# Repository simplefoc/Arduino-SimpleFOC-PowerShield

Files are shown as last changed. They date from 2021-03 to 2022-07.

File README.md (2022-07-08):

# Arduino *Simple**FOC** PowerShield* *v0.2* 
A powerful arduino shield for running BLDC motors using the FOC algorithm. This board is based on the [BTN8982](https://www.infineon.com/dgdl/Infineon-BTN8982TA-DS-v01_00-EN.pdf?fileId=db3a30433fa9412f013fbe32289b7c17) half bridges and can support currents up to 30 Amps continuous and 50Amps peak. Making it a board that can run virtually any BLDC motor.

<p align="">
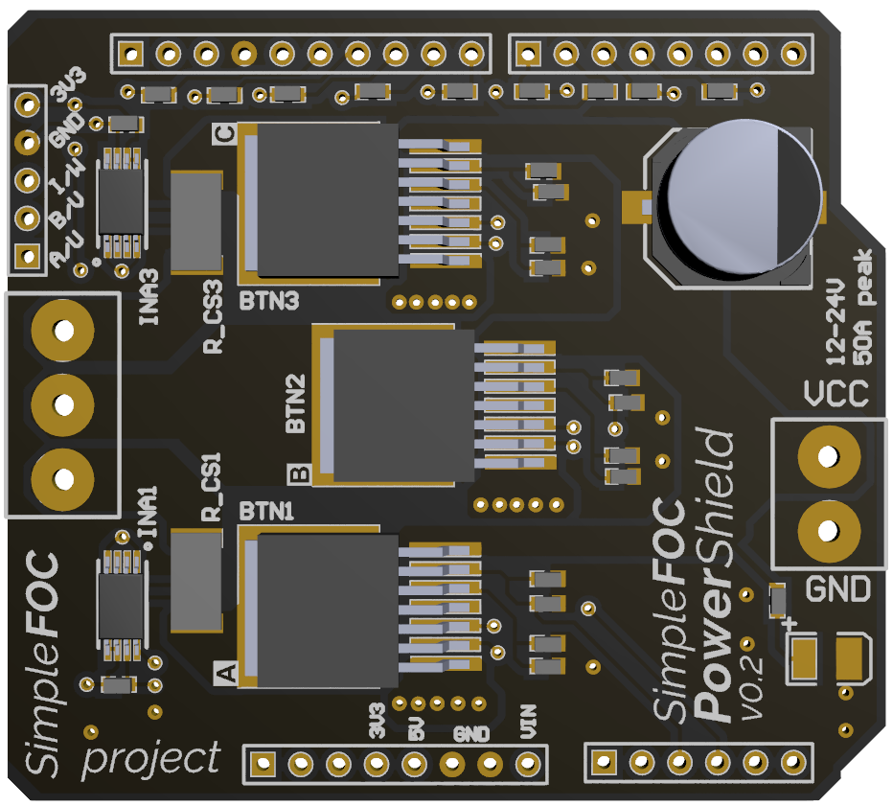
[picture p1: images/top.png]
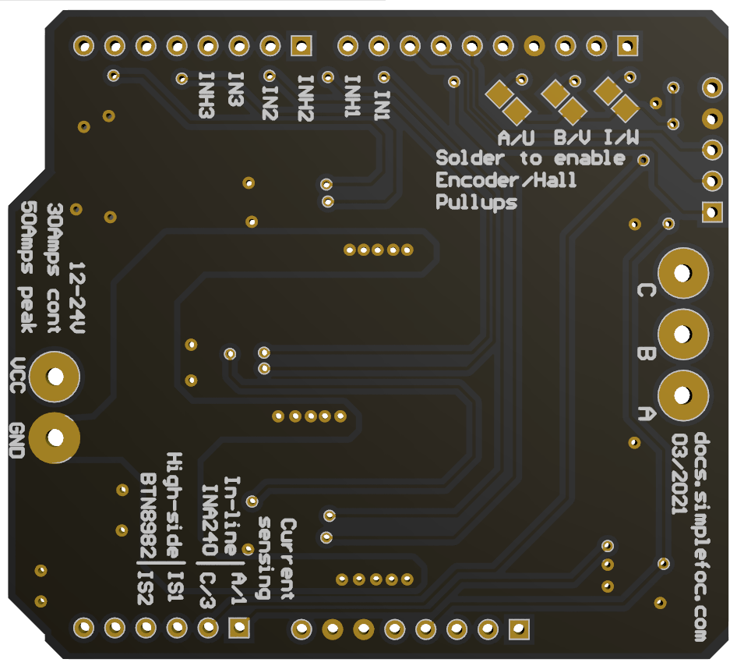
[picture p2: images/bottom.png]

</p>

<blockquote class="warning"><p class="heading"> ⚠️ BEWARE: BTN8982/IFX007T performance issues</p><p>BTN8982 and IFX007T drivers have been designed for DC motors and are based on old H-bridge technology. They have very long mosfet rise time (multiple microseconds) which in many cases presents a considerable part of the PWM duty cycle. When running the BLDC motors, precise PWM duty cycle setting is crucial for smooth and efficient operation. Therefore these drivers will not be able to provide very smooth operation on high frequency PWM (above 15kHz). Read more about it in the community thread: <a href="https://community.simplefoc.com/t/simplefoc-powershield/582">link</a>.<br> This performance constraint is the main reason why the <span class="simple">Simple<span class="foc">FOC</span> <b>Power</b>Shield</span> project has for now been put on hold, and although these boards are available through Aliexpress and some other platforms, they will not be available through simplefoc.com. <br><br></p><p>This does not mean that the board itself is not functional or that it will not work in your project though. It is still one of the cheapest (simplest) solutions out there for mid to high power BLDC control and with proper tuning of control loops you will still be able to get some good results with it.</p></blockquote>

### Features
- **Plug & play**: In combination with Arduino *Simple**FOC**library* - [github](https://github.com/simplefoc/Arduino-FOC)
- **Low-cost**: Fabrication price under €25/pcs - **will not be sold by silplefoc.com**
- **High-side current sensing**: - not yet supported by *Simple**FOC**library*
- **In-line current sensing**: - supported by *Simple**FOC**library*
- **Max power <500W**: max current 30A, power-supply 24V
- **Arduino headers**: Arduino UNO, Arduino MEGA, STM32 Nucleo boards, Aruidno DUE...
- **Small size**: 53mm x 60mm
- **Encoder/Hall sensors interface**: Integrated 3.3kΩ pullups (configurable)
- **Open Source**: 
   - Fully available fabrication files  
        - If never done it before, see a similar guide for *Simple**FOC**Shield*:  [how to make it yourself](https://docs.simplefoc.com/arduino_simplefoc_shield_fabrication)
   - Altium project
   - 3d model
   - schematics
    
#### Future features
- **Stackable**: running 2 motors in the same time
- **I2C interface**: Integrated 4.7kΩ pullups (configurable)
- **Configurable pinout**: Hardware configuration - soldering connections

> New version of the *Simple**FOC** PowerShield* is in the development at the moment (*v0.3*).
> The first versions are currently in testing. For more info check the [developmental branch](https://github.com/simplefoc/Arduino-SimpleFOC-PowerShield/tree/dev) 

### Pinouts
At this point ***Power**Shield* has fixed pinout.

#### Driver pinout
Signal | Description | Pin number
--- | --- | ----
IN1 | pwm 1 |	9
IN2 |  pwm 2 |	6
IN3 | 	pwm 3	 | 5 
INH1| enable 1 |	8
INH2 |	enable 2 |	7
INH3 |	enable  3	| 4

#### Current sensing pinout
Signal | Description | Pin number
--- | --- | ----
CS1 | in-line current sense - phase 1/A| A0
CS2 | in-line current sense - phase 3/C | A1
IS1 | high-side current sense - phase 1/A | A2
IS2 | high-side current sense - phase 2/B | A3

#### Sensor input pinout
Signal | Description | Pin number
--- | --- | ----
A/ U | Encoder A, Hall sensor U |	10
B/ V | Encoder B, Hall sensor V |	11
I/ W | Encoder C, Hall sensor W |	12

<p align="">
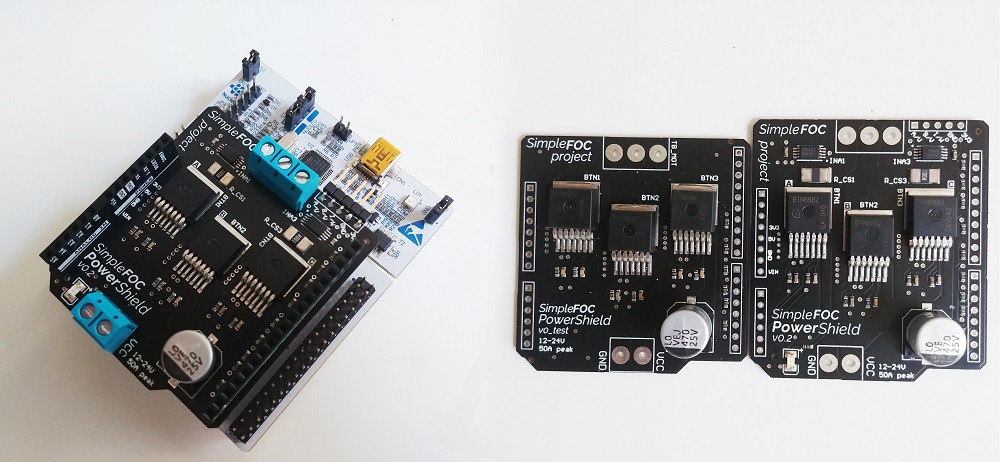
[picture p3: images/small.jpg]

</p>

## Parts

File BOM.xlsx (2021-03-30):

Name | Description | Designator | Quantity | Value | PackageReference
VEJ471M1ETR1010 |  | CAP_PWR | 1 | 470uF
INA240 |  | INA1, INA3 | 2
solder_connection |  | SCA, SCB, SCC | 3
TB002-500-03BE |  | TB_MOT | 1
TB002-500-02BE |  | TB_PWR | 1
BTN8982 | BTN8982 | BTN1, BTN2, BTN3 | 3
Cap Semi | Capacitor (Semiconductor SIM Model) | CBY1, CBY3 | 2 | 0.1uF | C0603
Cap Semi | Capacitor (Semiconductor SIM Model) | C_IS1, C_IS2, C_IS3 | 3 | 1nF | C0603
Cap Semi | Capacitor (Semiconductor SIM Model) | C_SR1, C_SR2, C_SR3 | 3 | 100nF | C1206
Header 5 | Header, 5-Pin | P_ENC | 1
Header 6 | Header, 6-Pin | P3 | 1
Header 8 | Header, 8-Pin | P1, P4 | 2
Header 10 | Header, 10-Pin | P2 | 1
Res3 | Resistor | R1, R2, R3, R4, R5, R6 | 6 | 10k | J1-0603
Res3 | Resistor | RPA, RPB, RPC | 3 | 3.3K | J1-0603
Res3 | Resistor | R_CS1, R_CS3 | 2 | 0.001 | RESC6332
Res3 | Resistor | R_IS1, R_IS2, R_IS3, RL | 4 | 1K | J1-0603
Res3 | Resistor | R_SR1, R_SR2, R_SR3 | 3 | 0.51k | J1-0603
LED3 | Typical BLUE SiC LED | D1 | 1 |  | 3.5X2.8X1.9

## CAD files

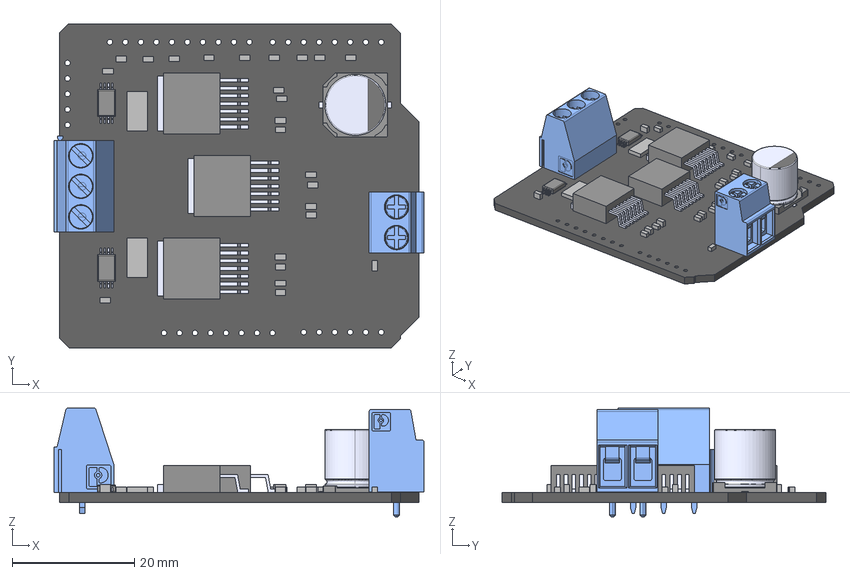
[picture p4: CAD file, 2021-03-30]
3d_model/SimpleFOCDriver.step
60.6 x 53.0 x 17.8 mm
Board
Extruded x 26
ina240 x 2
can_10x10_1
foot_cap_10x10_1 x 2
alelcap_sm10x10_1
2_RGB15238730
37753_RGB15238730
btn8982 x 3

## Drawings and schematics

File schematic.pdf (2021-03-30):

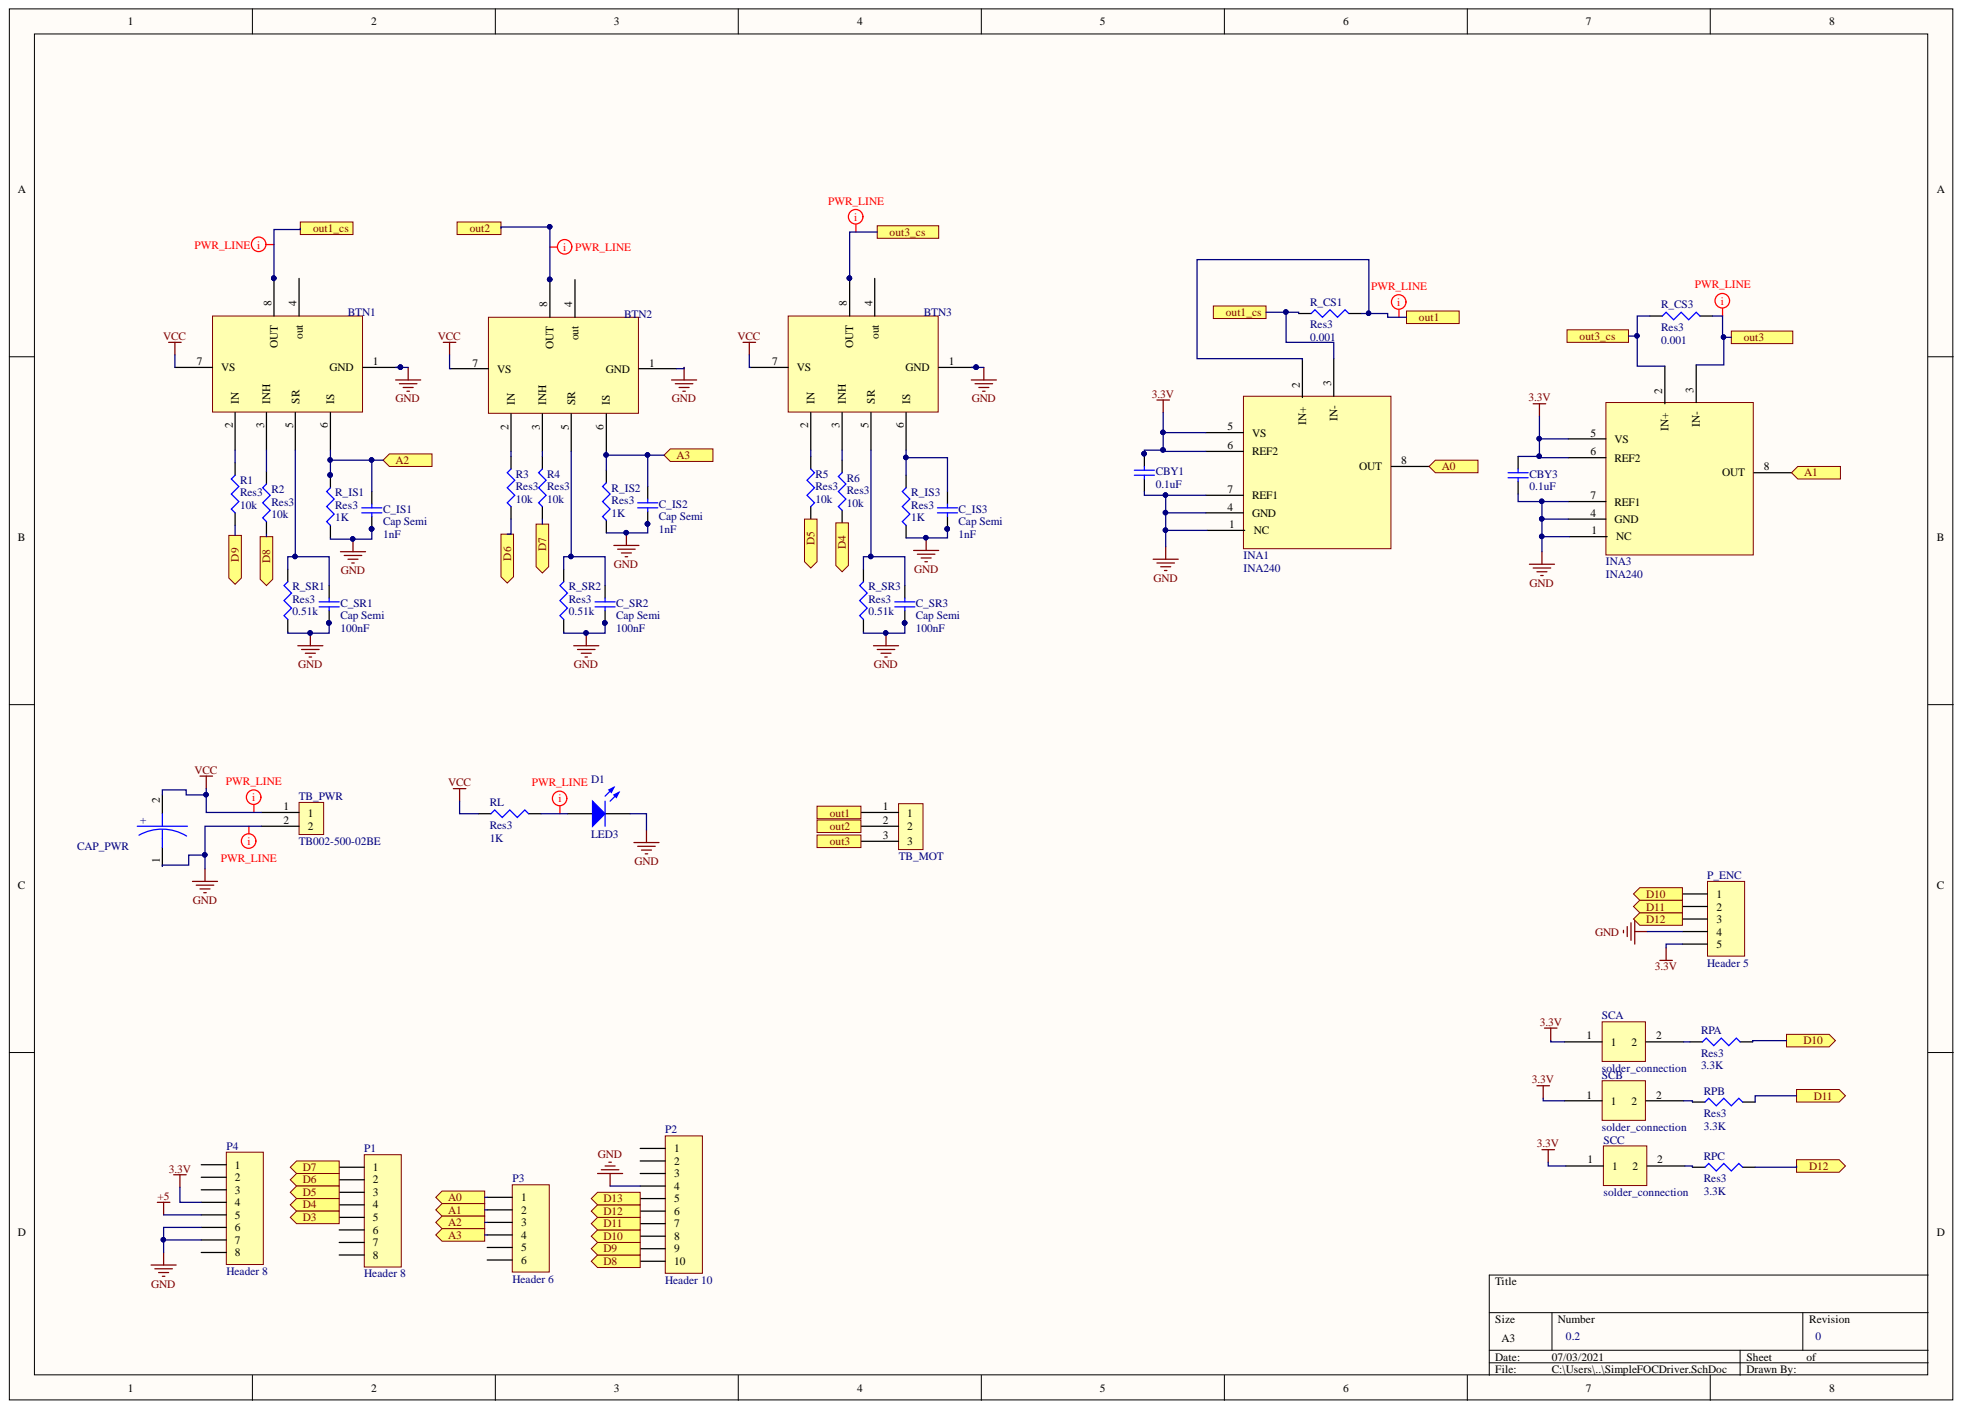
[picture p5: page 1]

GND 4

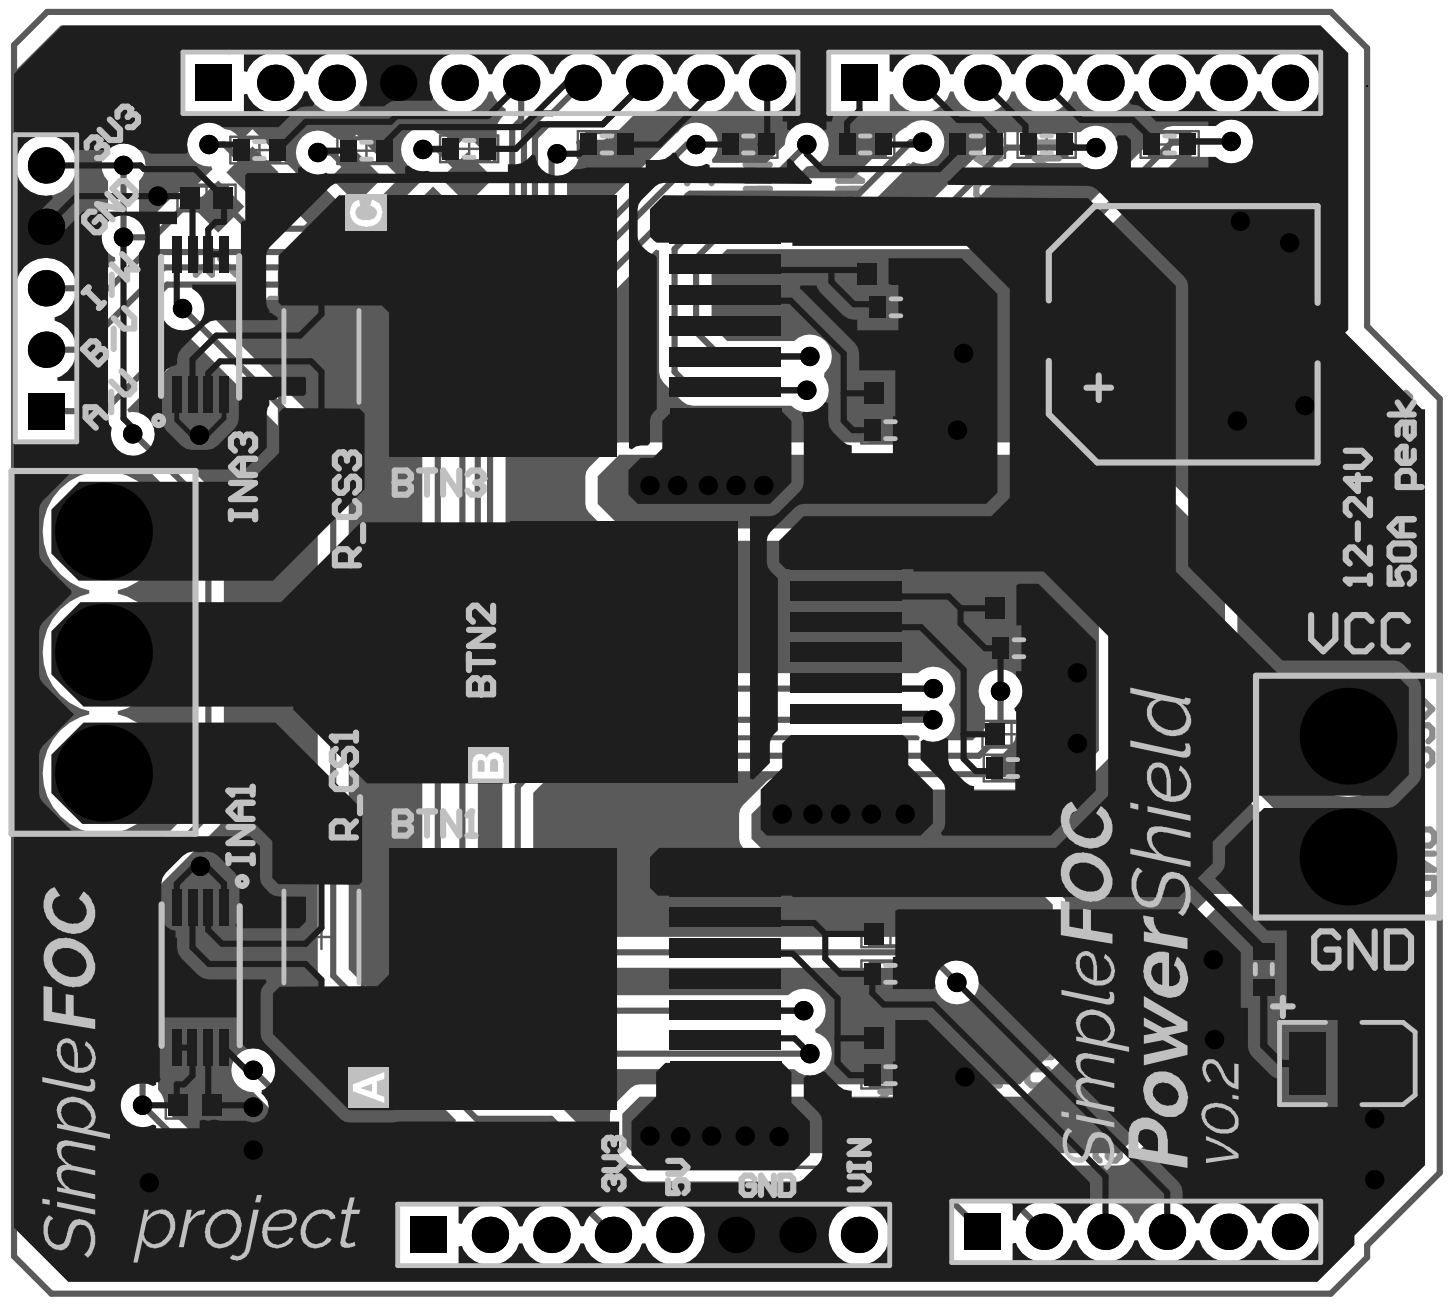
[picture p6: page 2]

Name | Description | Designator | Quantity | Value | PackageReference
VEJ471M1ETR101 0 | | CAP_PWR | 1 | 470uF
INA240 | | INA1, INA3 | 2
solder_connectio n | | SCA, SCB, SCC | 3
TB002-500-03BE | | TB_MOT | 1
TB002-500-02BE | | TB_PWR | 1
BTN8982 | BTN8982 | BTN1, BTN2, BTN3 | 3
Cap Semi | Capacitor (Semiconductor SIM Model) | CBY1, CBY3 | 2 | 0.1uF | C0603
Cap Semi | Capacitor (Semiconductor SIM Model) | C_IS1, C_IS2, C_IS3 | 3 | 1nF | C0603
Cap Semi | Capacitor (Semiconductor SIM Model) | C_SR1, C_SR2, C_SR3 | 3 | 100nF | C1206
Header 5 | Header, 5-Pin | P_ENC | 1
Header 6 | Header, 6-Pin | P3 | 1
Header 8 | Header, 8-Pin | P1, P4 | 2
Header 10 | Header, 10-Pin | P2 | 1
Res3 | Resistor | R1, R2, R3, R4, R5, R6 | 6 | 10k | J1-0603
Res3 | Resistor | RPA, RPB, RPC | 3 | 3.3K | J1-0603
Res3 | Resistor | R_CS1, R_CS3 | 2 | 0.001 | RESC6332
Res3 | Resistor | R_IS1, R_IS2, R_IS3, RL | 4 | 1K | J1-0603
Res3 | Resistor | R_SR1, R_SR2, R_SR3 | 3 | 0.51k | J1-0603
LED3 | Typical BLUE SiC LED | D1 | 1 | | 3.5X2.8X1.9

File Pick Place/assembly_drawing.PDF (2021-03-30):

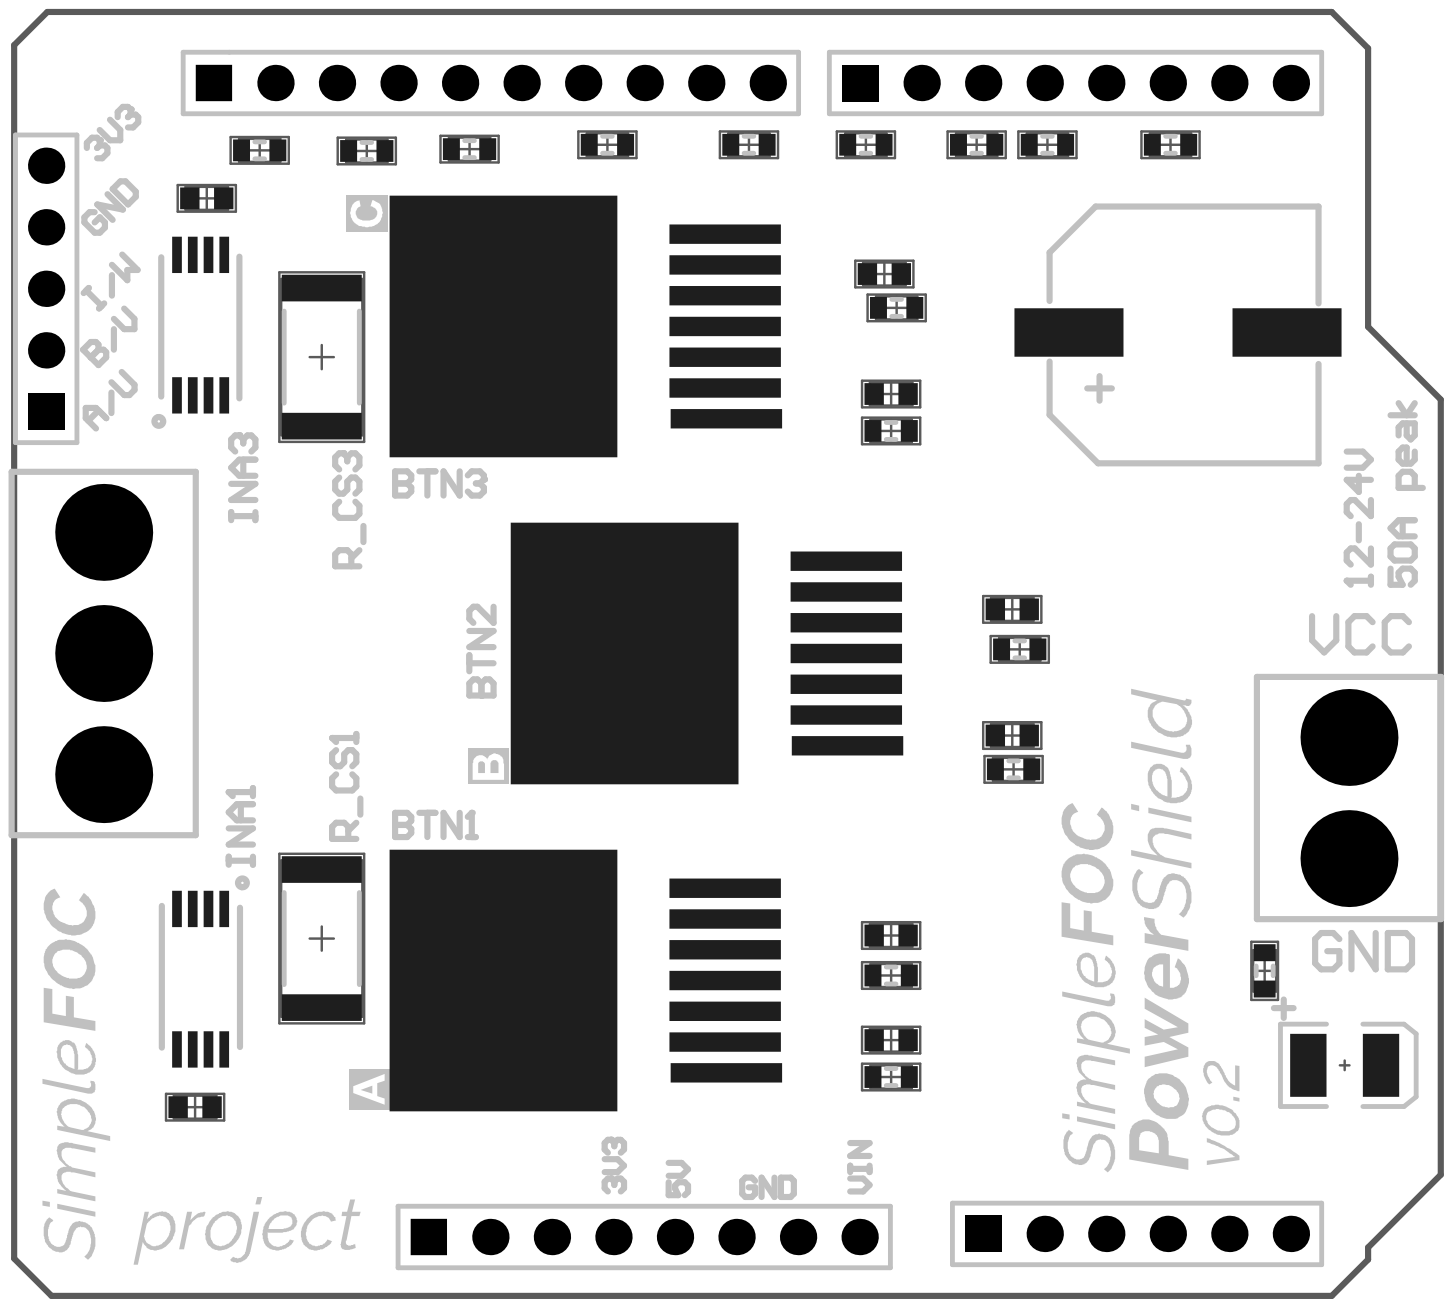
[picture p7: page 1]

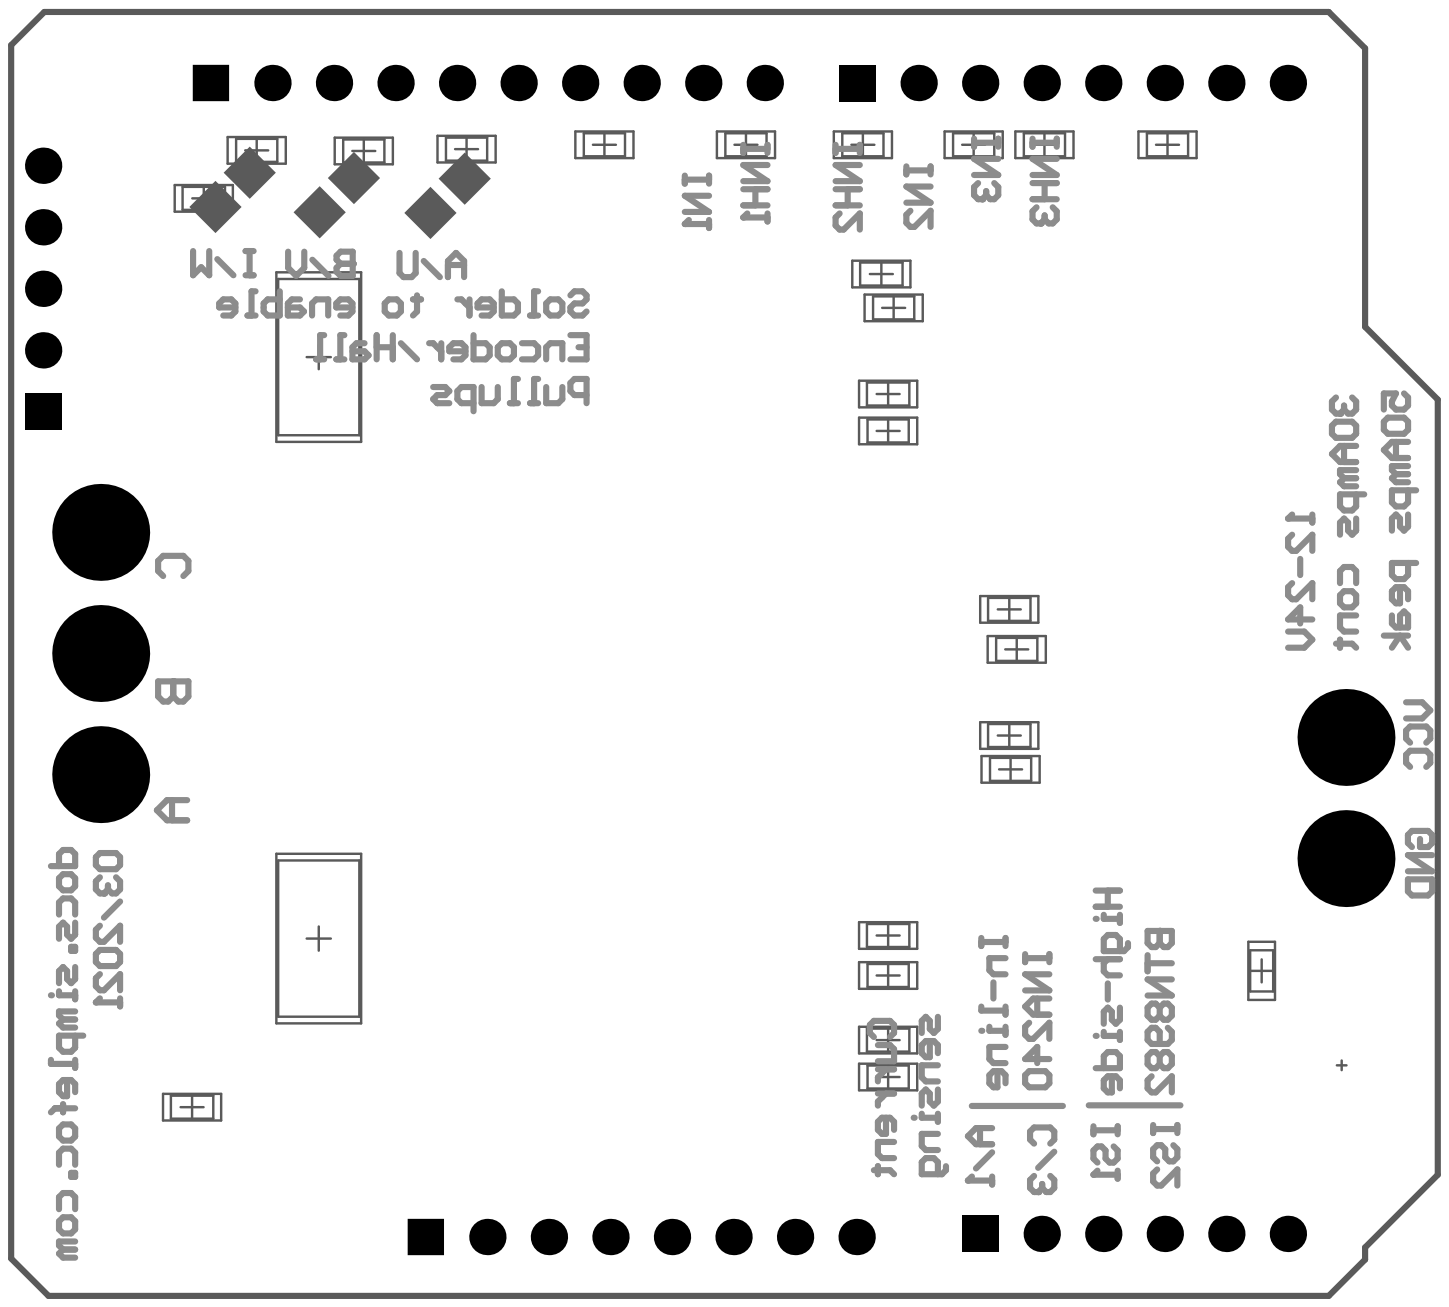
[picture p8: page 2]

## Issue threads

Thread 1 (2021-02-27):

Is there any example codes for the powershield?

candyriver, 2021-02-27:
I have get the board and fabricate it according to the tutorial, but I found the open_loop_velocity_control.ino  does not work.
Is there any code for the powershield?

askuric, 2021-02-28:
Hey @candyriver ,
I hope you've made it.

There are two things you can do:
Either enable the two additional INH pins in the Arduino setup function.
Or use the dev version of the library that has support for three enable pins.

It will be documented and releasef very soon :)

Closed 2021-02-28.

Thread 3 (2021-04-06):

Pinouts for the second Stack

haroldcy, 2021-04-06:
Stackable: running 2 motors in the same time
Pinouts: At this point PowerShield has fixed pinout.

how to play with the Pinouts for second stack?

askuric, 2021-04-07:
At this moment ( v0.2 ), this board is not stackable. The text you've quoted in in future releases.
I'll make sure to make it stackable for the next release v1. :)

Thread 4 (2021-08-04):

Schematic missing

bikeNomad, 2021-08-04:
`/schematic.pdf` is not a schematic. Please add an actual schematic for those of us who don't want to fire up a Windows VM just to run the Altium viewer.

askuric, 2021-08-04:
I am not sure that I follow. :slightly_smiling_face:
 `schematic.pdf` is a pdf file with the schematic exported from Altium. But you do not need altium to view it. You can open it with any pdf viewer or even with most of web browsers.

bikeNomad, 2021-08-04:
Sorry about that; I viewed the file in my web browser and the schematic page was blank. Downloading it revealed the schematic.
Thanks for your work!

askuric, 2021-08-04:
No worries, I am glad you like it!

Closed 2021-08-04.

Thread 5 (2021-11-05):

JLCPCB Assembly

seanray2k, 2021-11-05:
I've tried uploading both the BLM and the pick and place spreadsheets for JLCPCB, however the software doesn't recognize the information. Is there a way to reformat them?

askuric, 2021-11-05:
DId you first uplad the gerber files?
Here is a video explaining the procedure https://www.youtube.com/watch?v=sax_9sUgBuk&feature=emb_logo
It is for the si,plefocshield but the procedure is mostly the same.

seanray2k, 2021-11-05:
This was specifically for the simpleFOC power shield under your high performance boards. The gerber files were fine, however I was having difficulty troubleshooting the .csv files for the BOM and the Pick and Place, where the error was saying "No valid content found"

askuric, 2022-02-16:
I've stumbled across the same issue. It's due to the fact that JLCPCB has changed the requirement for the BOM file. They now require Footprint column. If you add an empty footprint column it will pass. I'll update the repo as soon as possible.

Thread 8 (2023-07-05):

The circuit board burned out before the current reached 10A

wood-kite, 2023-07-05:
I connected a 24V power supply and drove it through an ESP32. However, the circuit traces on the circuit board burned out before the current reached 10A. Should the design of this circuit board be further optimized? Otherwise, it won't be able to handle the intended 30A current.

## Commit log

2021-02-18 intiial commit
    [ArduinoFOC.PcbLib, BOM.xlsx, L6234PD.STEP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]
2021-03-30 FEAT version 0.2
    [ArduinoFOC.PcbLib, BOM.xlsx, L6234PD.STEP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]
2021-04-04 forgotten pick and place
    [Pick Place for SimpleFOCDriver.csv]
